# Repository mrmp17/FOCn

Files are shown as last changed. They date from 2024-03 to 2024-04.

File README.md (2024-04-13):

# FOCn - BLDC driver module

A *SimpleFOC* compatible medium-power BLDC driver module with Wi-Fi and Bluetooth connectivity
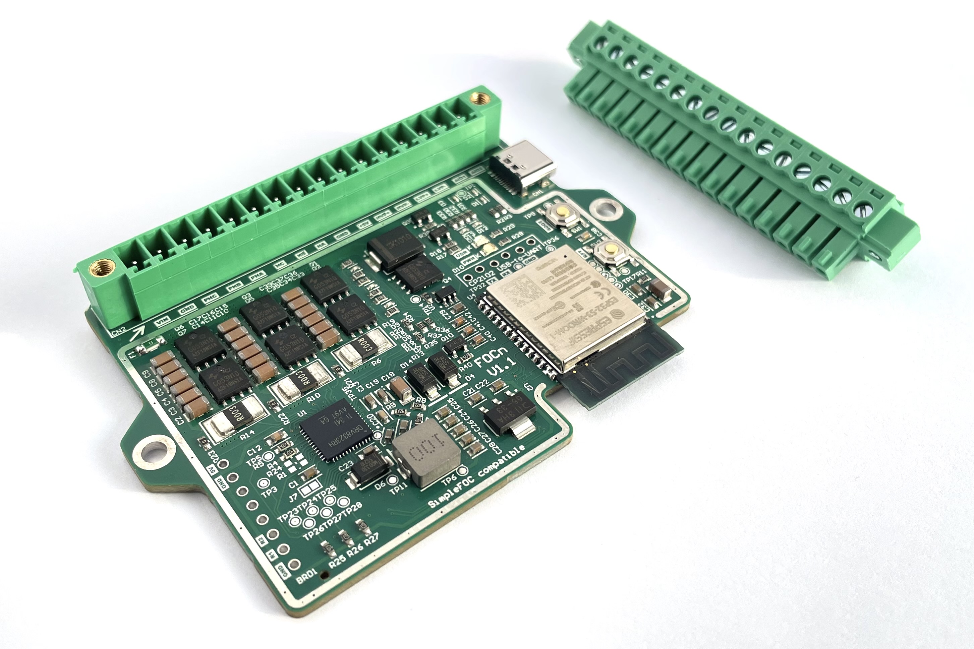
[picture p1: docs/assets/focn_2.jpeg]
FOCn photo


# Features

- Fully compatible with *SimpleFOC* field-oriented control library for easy programing
- High input voltage, up to 45V (up to 10s lithium battery)
- Up to 10A motor current without extra cooling
- Robust low-side current sensing for torque-control applications
- Supports hall sensors and encoders
- Based on ESP32-S3 dual core MCU
- Built-in USB-C and Wi-Fi / Bluetooth connectivity
- High power PWM output for solenoids, latches, magnetic brakes
- Power saving features for battery operation
- Pluggable terminal block for easy and robust connections

# Specs

- Input voltage: 9V-45V (3s - 10s lithium)
- Input current: 10A const., fuse protected
- Phase current: 10A const., 25A peak (more possible with enhanced cooling)
- Phase current measurement range: +-38A
- PWM output current: 5A average
- PWM load type: Supports inductive loads (flyback diode protection)
- Hall/encoder supply voltage: 5V
- Allowable external load on 5V supply: 300mA
- Idle current consumption (motor driver disabled, MCU seep sleep): <200uA
- Gate  driver with shunt amplifier: DRV8323

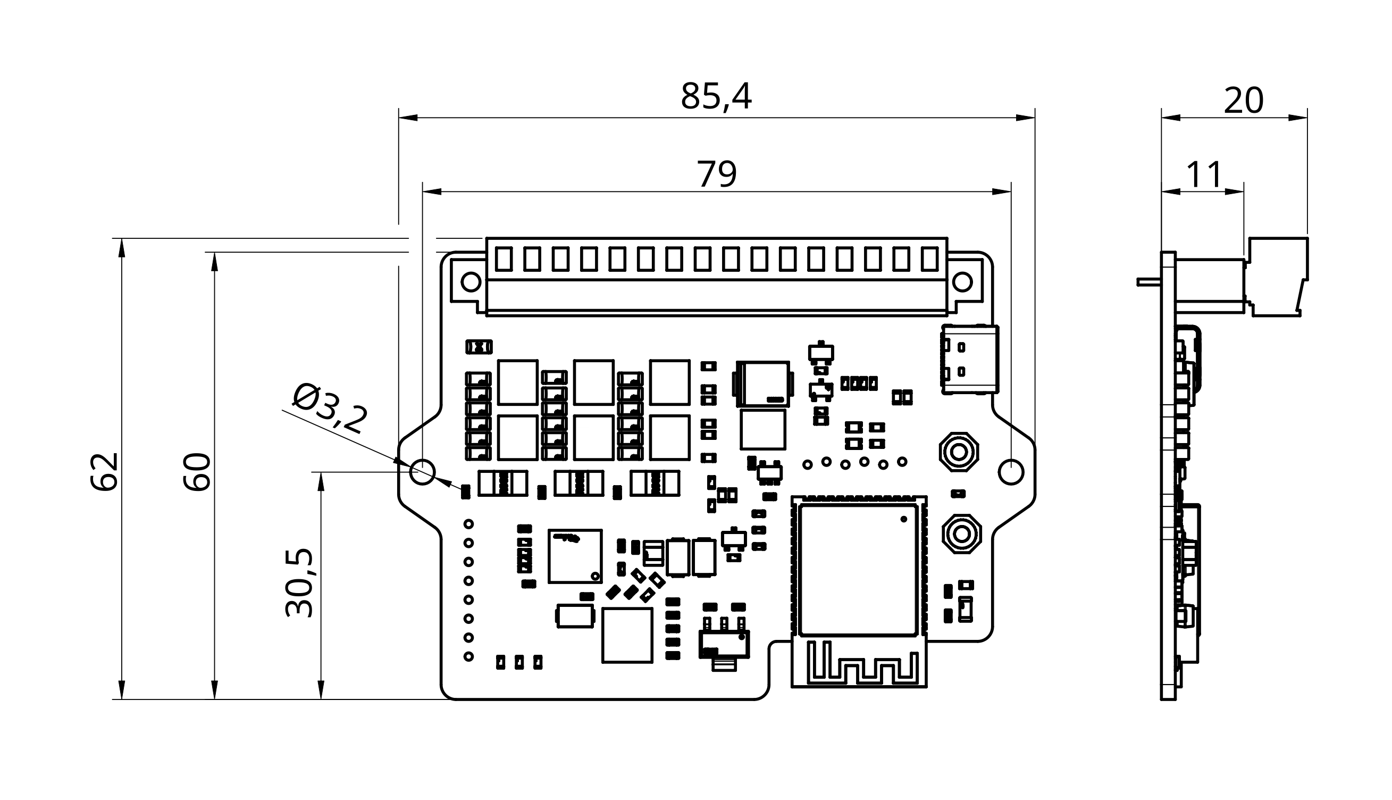
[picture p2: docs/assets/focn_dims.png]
Dimensions


# Where to get
*FOCn* is available on Tindie store.



# Getting started

### Connector pinout

Pin 1 is marked with an arrow near the connector. Compatible wire thickness is AWG18 to AWG16 (0.5 to 1.5 mm<sup>2</sup>).

| Pin | Marking | Description |
| --- | --- | --- |
| 1 | VIN | Supply voltage positive |
| 2 | GND | Supply voltage negative |
| 3 | PHC | Motor phase C |
| 4 | PHB | Motor phase B |
| 5 | PHA | Motor phase A |
| 6 | HC | Hall C / Encoder A/B |
| 7 | HB | Hall B / Encoder A/B |
| 8 | HA | Hall A / Encoder A/B |
| 9 | GND | Hall / Encoder supply voltage negative |
| 10 | +5V | Hall / Encoder supply voltage positive |
| 11 | HVP+ | High voltage PWM output positive (low side switched! HVP+ is connected to VIN) |
| 12 | HVP- | High voltage PWM output negative (low side switched!) |
| 13 | LVP+ | Low voltage PWM positive (high side switched) |
| 14 | LVP- | Low voltage PWM negative (high side switched) |
| 15 | AIO1 | Auxilary digital input 1 |
| 16 | AIO2 | Auxilary digital input 2 |

Pluggable screw terminal block part number: MAX MX15EDGKM-3.81-16P-GN01-Cu-Y-A

## Powering *FOCn*

Allowable input voltage is from 9V to 45V. Recomended cell count for lithium batteries is 3s to 10s, depending on your application. If using a power supply that is not a battery, carefully consider the effects of regenerative breaking. 

If your application requires high motor currents, consider adding an extra capacitor to the supply input, especially if other devices are powered by the same supply rail. 470uF 50V low ESR capacitor as close as possible to the input voltage terminals is recomended.

### Programming

*FOCn* can be programmed and debugged via the onboard USB-C which is connected to the ESP32’s native USB port. Programing should start automatically. If not, BOOT and RESET pushbuttons are available to control boot and programming. UART0 port is exposed on an unpopulated header.

### Motor connection

Motor phases should be connected at the screw terminal. Wiring should be as short as possible.

### Position sensors

Hall sensors or encoders with AB output can be connected to HA, HB, HC inputs. Inputs are filtered to avoid glitches caused by switching noise coupling to singal lines and strongly pulled up to 3.3V (MCU IO voltage). Pull-up voltage can be disabled from software for power saving during deep sleep.

HA, HB, HC inputs can also be used as general purpose IO by jumping jumpers J1, J2, J3 on the back of the PCB. Do this only if you know exactly what you are doing! **Warning: maximum allowable voltage input if jumpers are jumped is 3.3V!**

I2C encoders are also supported. Connect the data lines to AUX inputs.

### HVP output

High-voltage PWM is a low-side switched output designed for auxilary loads such as solenoids, magnetic brakes, indicator lights and other auxilary loads at up to 5A average current. Voltage is unregulated (same as input voltage to *FOCn*). Output can be used safely with inductive loads.

### LPV output

Low-voltage PWM is a high-side switched output designed for small auxilary loads such as sensors, indicator lights and communication modules. Up to 300mA is allocated for external loads. LVP can also be used to disable hall / encoder power for lower sleep current consumption.

### AUX inputs

Two auxilary inputs are available to be used with various sensors, safety switches, etc. Inputs are pulled up to 3.3V to support switches and open-drain outputs commonly used in industrial sensors. Maximum allowable voltage on auxilary inputs is 24V. To use auxilary inputs as outputs or data lines for I2C encoders, jump J4 and J5 on the back side of the PCB. This jumps the series protection resistor and provides a direct connection to MCU (3.3V signal level). **Warning: maximum allowable voltage input if jumpers are jumped is 3.3V!**

### RF keyfob receiver module

Keyfob remote module can be added to *FOCn*. The unpopulated header (bottom left) is designed to accept a HCS-300 rolling code receiver module. Two digital signals are connected to the MCU (D1 and D2). (module available here: https://www.parallax.com/product/key-fob-remote-and-receiver-pcb/)

### Wireless communication (Wi-Fi / BT)

The ESP32-S3 module has a built-in Wi-Fi and BLE modem which can be used to communicate with and control *FOCn*. ESP32-S3 also supports Espressif’s ESP-NOW protocol which is very suitable for BLDC control due to low latency and processing overhead. If possible, run communication and BLDC driver code on sepparate CPU cores.

### Adding extra cooling

If prolonged high motor currents (>10A) and/or high ambient temperatures (>35degC) are expected, aditional cooling should be added. This can be done by attaching a heat-dissipating body to the back of *FOCn* with a thermal pad (most heat is produced below the MOSFETs) or forced air cooling (fan)

### Using *FOCn* with smaller motors

In some cases, current sensing resolution might become an issue with low phase currents on small motors, as *FOCn* is designed for higher currents. This can be mitigated by changing the shunt resistor amplifier gain. By jumping *J7*, the gain is set to 40 (20 is default), which doubles the resolution. Keep in mind that this reduces the current measurement range to half the default value. Make sure to also modify the gains in *SimpleFOC* config.

### MCU pin mapping

| Name | GPIO | Description |
| --- | --- | --- |
| USR-LED | IO46 | User LED (yellow) |
| GDRV-INHA | IO12 | Phase A PWM |
| GDRV-INHB | IO13 | Phase B PWM |
| GDRV-INHC | IO14 | Phase C PWM |
| SHUNT-AMP-OUT-A | IO4 | Phase A current analog signal |
| SHUNT-AMP-OUT-B | IO6 | Phase B current analog signal |
| SHUNT-AMP-OUT-C | IO5 | Phase C current analog signal |
| HVPWM-CTRL | IO35 | HVPWM PWM control signal |
| LVPWM-CTRL | IO47 | LVPWM PWM control signal |
| N-HALL-PU-EN | IO48 | Hall pullup voltage enaple (active low) |
| GDRV-ENABLE | IO41 | Gate driver enable (enables BLDC driver) |
| GDRV-nFAULT | IO42 | Gate driver fault flag (active low) |
| GDRV-AMP-CAL | IO40 | Shunt amplifier offset calibration trigger |
| HALL-A | IO38 | Hall A signal |
| HALL-B | IO37 | Hall B signal |
| HALL-C | IO36 | Hall C signal |
| AUX-1 | IO10 | AUX-1 signal |
| AUX-2 | IO9 | AUX-2 signal |
| VIN-MEAS | IO8 | Suply voltage measurement analog input |
| RF-REMOTE-D1 | IO1 | RF remote module D1 signal |
| RF-REMOTE-D1 | IO2 | RF remote module D2 signal |
| TP-IO3 | IO3 | TP36 test point |
| TP-IO7 | IO7 | TP31 test point |
| TP-IO11 | IO11 | TP32 test point |
| TP-IO15 | IO15 | TP33 test point |
| TP-IO16 | IO16 | TP34 test point |
| TP-IO17 | IO17 | TP29 test point |
| TP-IO18 | IO18 | TP30 test point |

### Example project
Example *PlatformIO* project is available in the *Examples* folder. It implements basic control of a hoverboard hub motor (with phase current control) and demonstrates basic usage of *FOCn*. As the motor control input, a standard RC PWM signal is used. When developing your own projects, it is recomended to use the *PlatformIO* board file used in the example project (*/boards/FOCn_board.json*).

### Use case example
*FOCn* is used as a controller in my HoverGate project - an outdoor wing gate automated with hoverboard motors. 

Demonstration video: https://www.youtube.com/watch?v=YPjKRgDzimE

Code: https://github.com/mrmp17/HoverGate-V2-FW

Each gate wing has a *FOCn* module driving a hoverboard motor that moves the gate. To synchronize the movements, both *FOCns* communicate via ESP-NOW protocol. One of the modules also connects to Wi-Fi and is accessible on Home Assistant via MQTT. There is also an RF receiver module connected to one module so that the gates can be opened by a keyfob remote. To lock the gate wings in place when closed, a magnetic door latch is connected to the *FOCn's* high voltage PWM output.

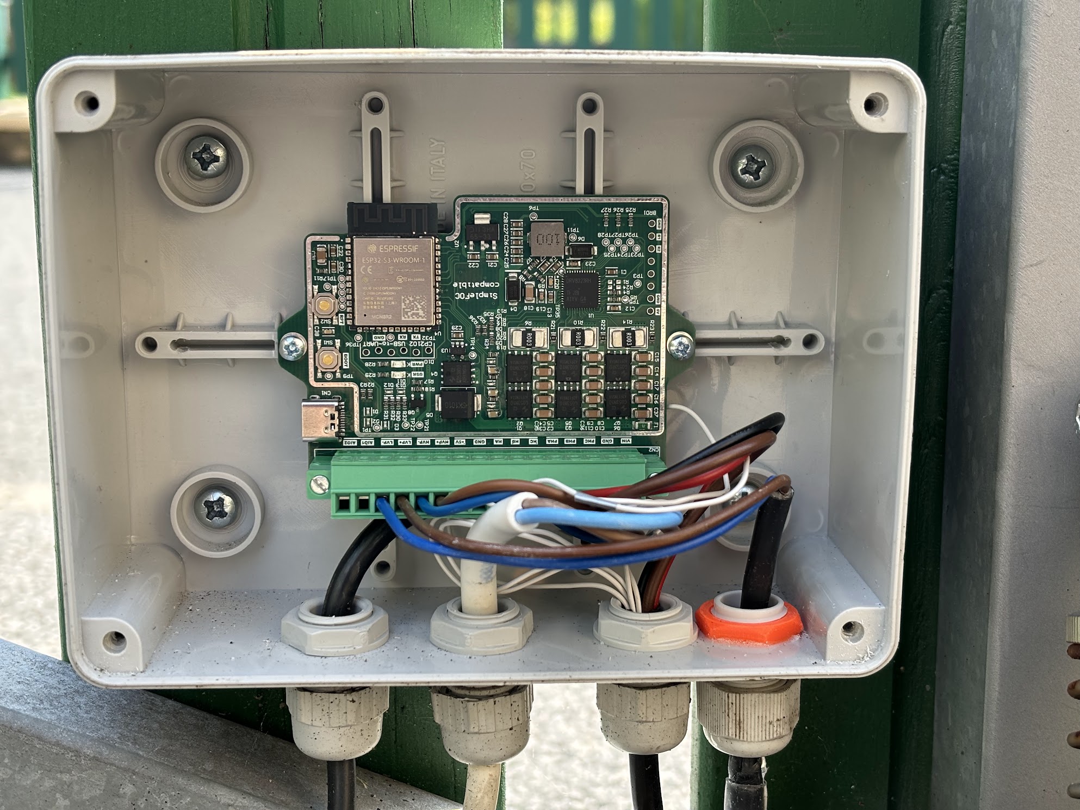
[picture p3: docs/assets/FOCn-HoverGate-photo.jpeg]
FOCn HoverGate photo


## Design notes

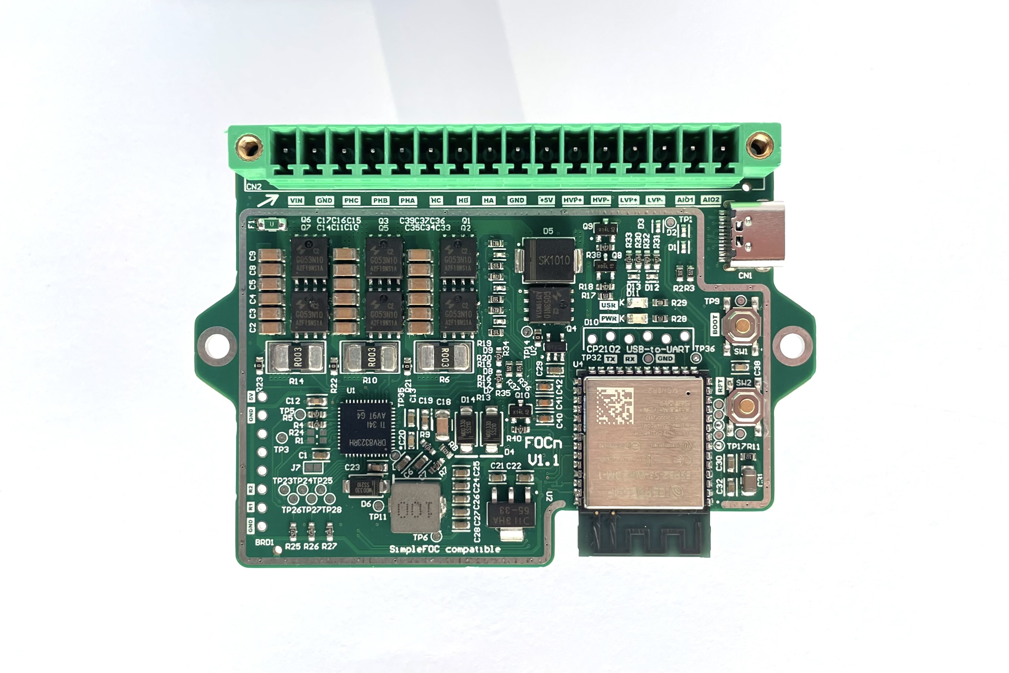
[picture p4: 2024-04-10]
docs/assets/focn_1.jpeg

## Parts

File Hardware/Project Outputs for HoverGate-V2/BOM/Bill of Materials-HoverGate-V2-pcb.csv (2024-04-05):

Comment | Description | Designator | Footprint | LibRef | Quantity | LCSC
HCS-301-rolling-code-rx |  | BRD1 | HC301-module | HCS-301-rolling-code-rx | 1
CL10A105KB8NNNC | CAP CER 1UF 50V X5R 0603 | C1, C6, C7, C13, C21, C22, C24, C25, C26, C27, C28, C29, C30, C32 | FP-CL10B105KO8NNNC-IPC_B | CMP-2000-06093-2 | 14 | C15849
CL31A106KBHNNNE | CAP CER 10UF 50V X5R 1206 | C2, C3, C4, C5, C8, C9, C10, C11, C14, C15, C16, C17, C33, C34, C35, C36, C37, C39 | FP-CL31-IPC_C | CMP-13271-000016-1 | 18 | C13585
CL10B104KC8NNNC | Cap Ceramic 100nF 100V X7R ±10% Pad SMD 0603 +125°C T/R | C12, C19, C23 | FP-CL10-IPC_A | CMP-13271-004036-1 | 3
GRM32ER71J106KA12L | CAP CER 10UF 63V X7R 1210 | C18 | FP-GRM32E-0_2-0_3-MFG | CMP-2000-07458-2 | 1 | C437568
AC0603KRX7R0BB473 | CAP CER 0.047UF 100V X7R 0603 | C20, C38 | FP-AC0603-IPC_B | CMP-03422-001184-1 | 2 | C469624
CL31A226KPHNNNE | Cap Ceramic 22uF 10V X5R ±10% SMD 1206 | C31 | FP-CL31-IPC_B | CMP-13271-002604-1 | 1 | C5672
0603B151K500NT | CAP CER 150p 50V X7R 0603 | C40, C41, C42 | FP-AC0603-IPC_B | CMP-03422-001184-1 | 3 | C1594
XKB U262-161N-4BVC11 | USB Type-C connector, USB-2.0, 16 pins | CN1 | XKB U262-161N-4BVC11 | XKB U262-161N-4BVC11 | 1 | C319148
MAX MX15EDGVM-3.81-16P-GN01-Cu-A | Board connector for 16 pin pluggable screw terminal | CN2 | MAX MX15EDGVM-3.81-16P-GN01-Cu-A | MAX MX15EDGVM-3.81-16P-GN01-Cu-A | 1 | C5188240
CP2102 USB-A-to-UART adapter connector |  | CN3 | CP2102 USB-A-to-UART adapter connector | CP2102 USB-A-to-UART adapter connector | 1
LXES15AAA1-133 | TVS DIODE 15V 1005 | D1, D2, D3, D7, D8, D9, D12, D13 | FP-LXES15-IPC_A | CMP-06195-000011-1 | 8 | C191267
B1100-13-F | Schottky Barrier Rectifier, 100 V, 1 A, -65 to 150 degC, 2-Pin SMA, RoHS, Tape and Reel | D4, D6, D14 | DIOD-SMA-2_V | CMP-2000-05882-1 | 3 | C110106
SK1010C | DIODE SCHOTTKY 100V 10A SMC | D5 | FP-SMC-MFG | CMP-2000-05097-3 | 1 | C3018527
KT-0805G | KT-0805G LED Green | D10 | LED_0805 | LED Green | 1 | C2297
KT-0805Y | LED Yellow KT-0805Y | D11 | LED_0805 | LED Blue | 1 | C2296
0458005.DR | FUSE BOARD MOUNT 5A 75VDC 1206 | F1 | FP-0469-IPC_B | CMP-08605-000100-1 | 1 | C187561
SolderJumperV2 |  | J1, J2, J3, J4, J5, J6, J7 | AislerRule_SolderJumper_1mm | SolderJumperV2 | 7
CYA0630-10UH | SMD Power inductio, 10uH 4A | L1 | CYA0630-10UH | PowerInductor | 1 | C5189958
HYG053N10NS1C2 | 100V 95A 4.6mOhm N-channel mosfet | Q1, Q2, Q3, Q4, Q5, Q6, Q7 | PDFN5*6-8L | HYG053N10NS1C2 | 7
BM3402 | BORN BM3402 MOSFET N-CH 30V 5.1A SOT23 | Q8 | FP-SOT23-IPC_B | CMP-83955-000006-1 | 1 | C431498
AO3401A | P-Channel MOSFET, 30 V, 4 A, -55 to 150 degC, 3-Pin SOT-23-3L, RoHS, Tape and Reel | Q9, Q10 | AO-SOT-23-3L_V | CMP-2000-05778-1 | 2
DNP | RES SMD 47K OHM 1% 1/10W 0603 | R1, R24 | FP-RC0603FR-0747KL-MFG | CMP-1659-00055-2 | 2 | C105579
0603WAF5101T5E |  | R2, R3, R11, R13, R16, R17, R20, R28, R36, R37 | RESC1608X55X30NL15T15 | CMP-2000-00540-1 | 10 | C23186
RC0603FR-0747KL | RES SMD 47K OHM 1% 1/10W 0603 | R4, R5, R7, R9, R18, R25, R26, R27, R30, R31, R32, R33, R34, R35, R38, R40 | FP-RC0603FR-0747KL-MFG | CMP-1659-00055-2 | 16 | C105579
LR2512D-3W-3mR-1% | 2512 3mohm shunt | R6, R10, R14 | FPR_CRF2512_R0 | R | 3 | C500737
0603WAF2203T5E |  | R8 | RESC1608X55X30NL15T15 | CMP-2000-00540-1 | 1 | C22961
0603WAF8200T5E |  | R12, R15, R19 | RESC1608X55X30NL15T15 | CMP-2000-00540-1 | 3 | C23253
0603WAF0000T5E | 0R resistor | R21, R22, R23, R39 | FPR_0603_R_R0 | R | 4
0603WAF1001T5E |  | R29 | RESC1608X55X30NL15T15 | CMP-2000-00540-1 | 1 | C21190
TS-1187A-B-A-B | XKB TS-1187A-B-A-B C318884 | SW1, SW2 | ESWI-TL3342F160QG_V | CMP-1696-00003-1 | 2 | C318884
test point 1.5mm | Test point ,1.5mm diameter, no hole | TP1, TP2, TP3, TP4, TP5, TP6, TP7, TP8, TP9, TP10, TP11, TP12, TP13, TP14, TP15, TP16, TP17, TP18, TP19, TP20, TP23, TP24, TP25, TP26, TP27, TP28, TP29, TP30, TP31, TP32, TP33, TP34, TP35, TP36 | TP1_FULL | Test Point | 34
DRV8323RHRGZT | IC MTR DRV MULTIPHAS 6-60V 48QFN | U1 | FP-RGZ0048A-IPC_A | CMP-04912-000089-1 | 1
AP7365-33EG-13 | IC REG LIN 3.3V 600MA SOT223-3 | U2 | FP-SOT223-IPC_C | CMP-12756-000040-1 | 1
SLM27517 | mosfet gate driver | U3 | Diodes Inc SOT25 | SLM27517 | 1
ESP32-S3-WROOM-1-N8R2 | WiFi 802.11a/b/g/n, Bluetooth v5.0 Transceiver Module 2.4GHz Antenna Not Included - | U4 | XCVR_ESP32-S3-WROOM-1-N8R2 | ESP32-S3-WROOM-1-N8R2 | 1

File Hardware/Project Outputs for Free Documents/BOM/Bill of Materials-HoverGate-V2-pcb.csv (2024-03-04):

Comment | Description | Designator | Footprint | LibRef | Quantity | LCSC
HCS-301-rolling-code-rx |  | BRD1 | HC301-module | HCS-301-rolling-code-rx | 1
CL10A105KB8NNNC | CAP CER 1UF 50V X5R 0603 | C1, C6, C7, C13, C21, C22, C24, C25, C26, C27, C28, C29, C30, C32, C33, C34 | FP-CL10B105KO8NNNC-IPC_B | CMP-2000-06093-2 | 16 | C15849
GRM32ER71J106KA12L | CAP CER 10UF 63V X7R 1210 | C2, C3, C4, C5, C8, C9, C10, C11, C14, C15, C16, C17, C18, C35, C36, C37 | FP-GRM32E-0_2-0_3-MFG | CMP-2000-07458-2 | 16 | C437568
CL10B104KC8NNNC | Cap Ceramic 100nF 100V X7R ±10% Pad SMD 0603 +125°C T/R | C12, C19, C23 | FP-CL10-IPC_A | CMP-13271-004036-1 | 3
AC0603KRX7R0BB473 | CAP CER 0.047UF 100V X7R 0603 | C20, C38 | FP-AC0603-IPC_B | CMP-03422-001184-1 | 2 | C469624
CL31A226KPHNNNE | Cap Ceramic 22uF 10V X5R ±10% SMD 1206 | C31 | FP-CL31-IPC_B | CMP-13271-002604-1 | 1 | C5672
XKB U262-161N-4BVC11 | USB Type-C connector, USB-2.0, 16 pins | CN1 | XKB U262-161N-4BVC11 | XKB U262-161N-4BVC11 | 1 | C319148
MAX MX15EDGVM-3.81-16P-GN01-Cu-A | Board connector for 16 pin pluggable screw terminal | CN2 | MAX MX15EDGVM-3.81-16P-GN01-Cu-A | MAX MX15EDGVM-3.81-16P-GN01-Cu-A | 1 | C5188240
CP2102 USB-A-to-UART adapter connector |  | CN3 | CP2102 USB-A-to-UART adapter connector | CP2102 USB-A-to-UART adapter connector | 1
LXES15AAA1-133 | TVS DIODE 15V 1005 | D1, D2, D3, D7, D8, D9, D12, D13 | FP-LXES15-IPC_A | CMP-06195-000011-1 | 8 | C191267
B1100-13-F | Schottky Barrier Rectifier, 100 V, 1 A, -65 to 150 degC, 2-Pin SMA, RoHS, Tape and Reel | D4, D6 | DIOD-SMA-2_V | CMP-2000-05882-1 | 2 | C110106
SK1010C | DIODE SCHOTTKY 100V 10A SMC | D5 | FP-SMC-MFG | CMP-2000-05097-3 | 1 | C3018527
LED Green | Generic LED Green | D10 | LED_0805 | LED Green | 1
LED Blue | LED Blue | D11 | LED_0805 | LED Blue | 1
0458005.DR | FUSE BOARD MOUNT 5A 75VDC 1206 | F1 | FP-0469-IPC_B | CMP-08605-000100-1 | 1 | C187561
SolderJumperV2 |  | J1, J2, J3, J4, J5 | AislerRule_SolderJumper_1mm | SolderJumperV2 | 5
CYA0630-10UH | SMD Power inductio, 10uH 4A | L1 | CYA0630-10UH | PowerInductor | 1 | C5189958
HYG053N10NS1C2 | 100V 95A 4.6mOhm N-channel mosfet | Q1, Q2, Q3, Q4, Q5, Q6, Q7 | PDFN5*6-8L | HYG053N10NS1C2 | 7
BM3402 | BORN BM3402 MOSFET N-CH 30V 5.1A SOT23 | Q8 | FP-SOT23-IPC_B | CMP-83955-000006-1 | 1 | C431498
DNP | RES SMD 47K OHM 1% 1/10W 0603 | R1, R24 | FP-RC0603FR-0747KL-MFG | CMP-1659-00055-2 | 2 | C105579
0603WAF5101T5E |  | R2, R3, R8, R9, R11, R12, R13, R15, R16, R17, R19, R20, R28, R29, R36, R37 | RESC1608X55X30NL15T15 | CMP-2000-00540-1 | 16 | C23186
RC0603FR-0747KL | RES SMD 47K OHM 1% 1/10W 0603 | R4, R5, R7, R18, R25, R26, R27, R30, R31, R32, R33, R34, R35 | FP-RC0603FR-0747KL-MFG | CMP-1659-00055-2 | 13 | C105579
LR2512D-3W-3mR-1% | 2512 3mohm shunt | R6, R10, R14 | FPR_CRF2512_R0 | R | 3 | C500737
0R | 0R resistor | R21, R22, R23 | FPR_0603_R_R0 | R | 3
TS-1187A-B-A-B | XKB TS-1187A-B-A-B C318884 | SW1, SW2 | ESWI-TL3342F160QG_V | CMP-1696-00003-1 | 2 | C318884
test point 1.5mm | Test point ,1.5mm diameter, no hole | TP1, TP2, TP3, TP4, TP5, TP6, TP7, TP8, TP9, TP10, TP11, TP12, TP13, TP14, TP15, TP16, TP17, TP18, TP19, TP20, TP21, TP22, TP23, TP24, TP25, TP26, TP27, TP28, TP29, TP30, TP31, TP32, TP33, TP34, TP35, TP36 | TP1_FULL | Test Point | 36
DRV8323RHRGZT | IC MTR DRV MULTIPHAS 6-60V 48QFN | U1 | FP-RGZ0048A-IPC_A | CMP-04912-000089-1 | 1
AZ1117CH-3.3TRG1 | IC REG LINEAR 3.3V 800MA SOT223 | U2 | FP-SOT223-IPC_B | CMP-12756-000028-1 | 1 | C92102
MCP1402T-E/OT | Tiny 500 mA, High-Speed Power MOSFET Driver, Non Inverting, Extended Temperature, Tape and Reel | U3 | SOT-23-OT5_L | CMP-0137-00408-1 | 1 | C128573
ESP32-S3-WROOM-1-N8R2 | WiFi 802.11a/b/g/n, Bluetooth v5.0 Transceiver Module 2.4GHz Antenna Not Included - | U4 | XCVR_ESP32-S3-WROOM-1-N8R2 | ESP32-S3-WROOM-1-N8R2 | 1
AZ1117CH-5.0TRG1 | IC REG LINEAR 5.0V 800MA SOT223 | U5 | FP-SOT223-IPC_B | CMP-12756-000028-1 | 1 | C99342

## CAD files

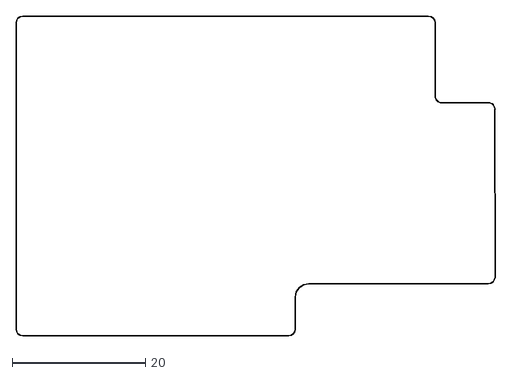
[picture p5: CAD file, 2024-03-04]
Hardware/3d/fancyedge.dxf
72.0 x 48.0

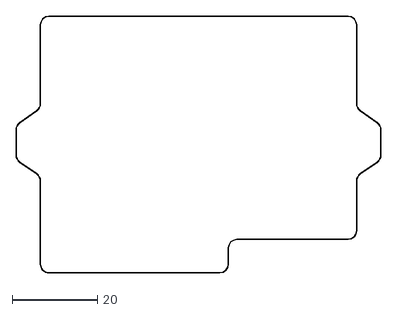
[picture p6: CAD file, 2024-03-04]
Hardware/3d/PCB-shape.dxf
85.4 x 60.0

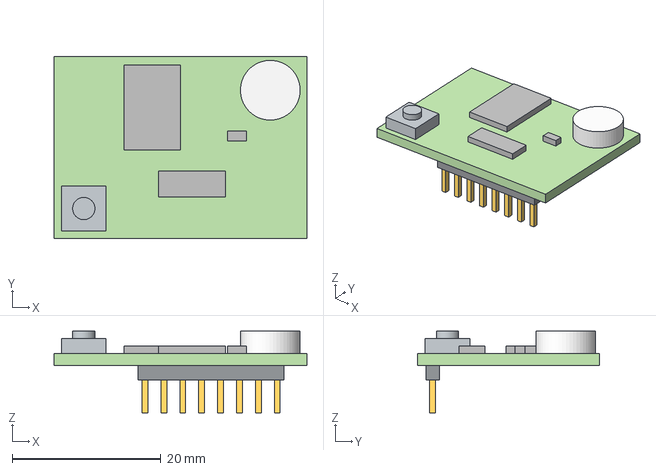
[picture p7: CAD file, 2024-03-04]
Hardware/3d/hcs301-module.step
34.0 x 24.4 x 11.0 mm

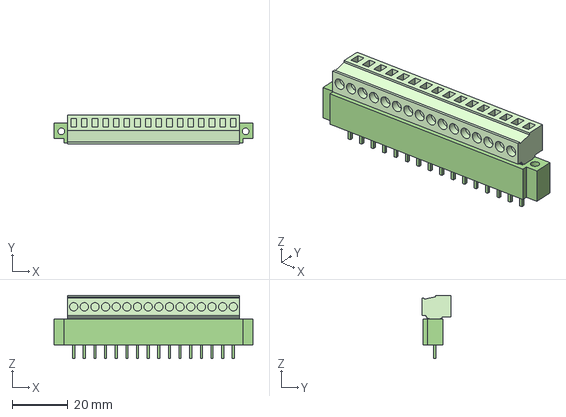
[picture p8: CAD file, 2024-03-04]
Hardware/3d/MAX MX15EDGVM-3.81-16P.step
71.2 x 10.4 x 22.7 mm

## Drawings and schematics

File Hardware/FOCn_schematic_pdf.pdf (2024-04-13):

# VBUS A9 SHELL SHELL SHELL SHELL TYPE-C USB-2.0 CN1

# USB-C connector (ESP debug & comms)

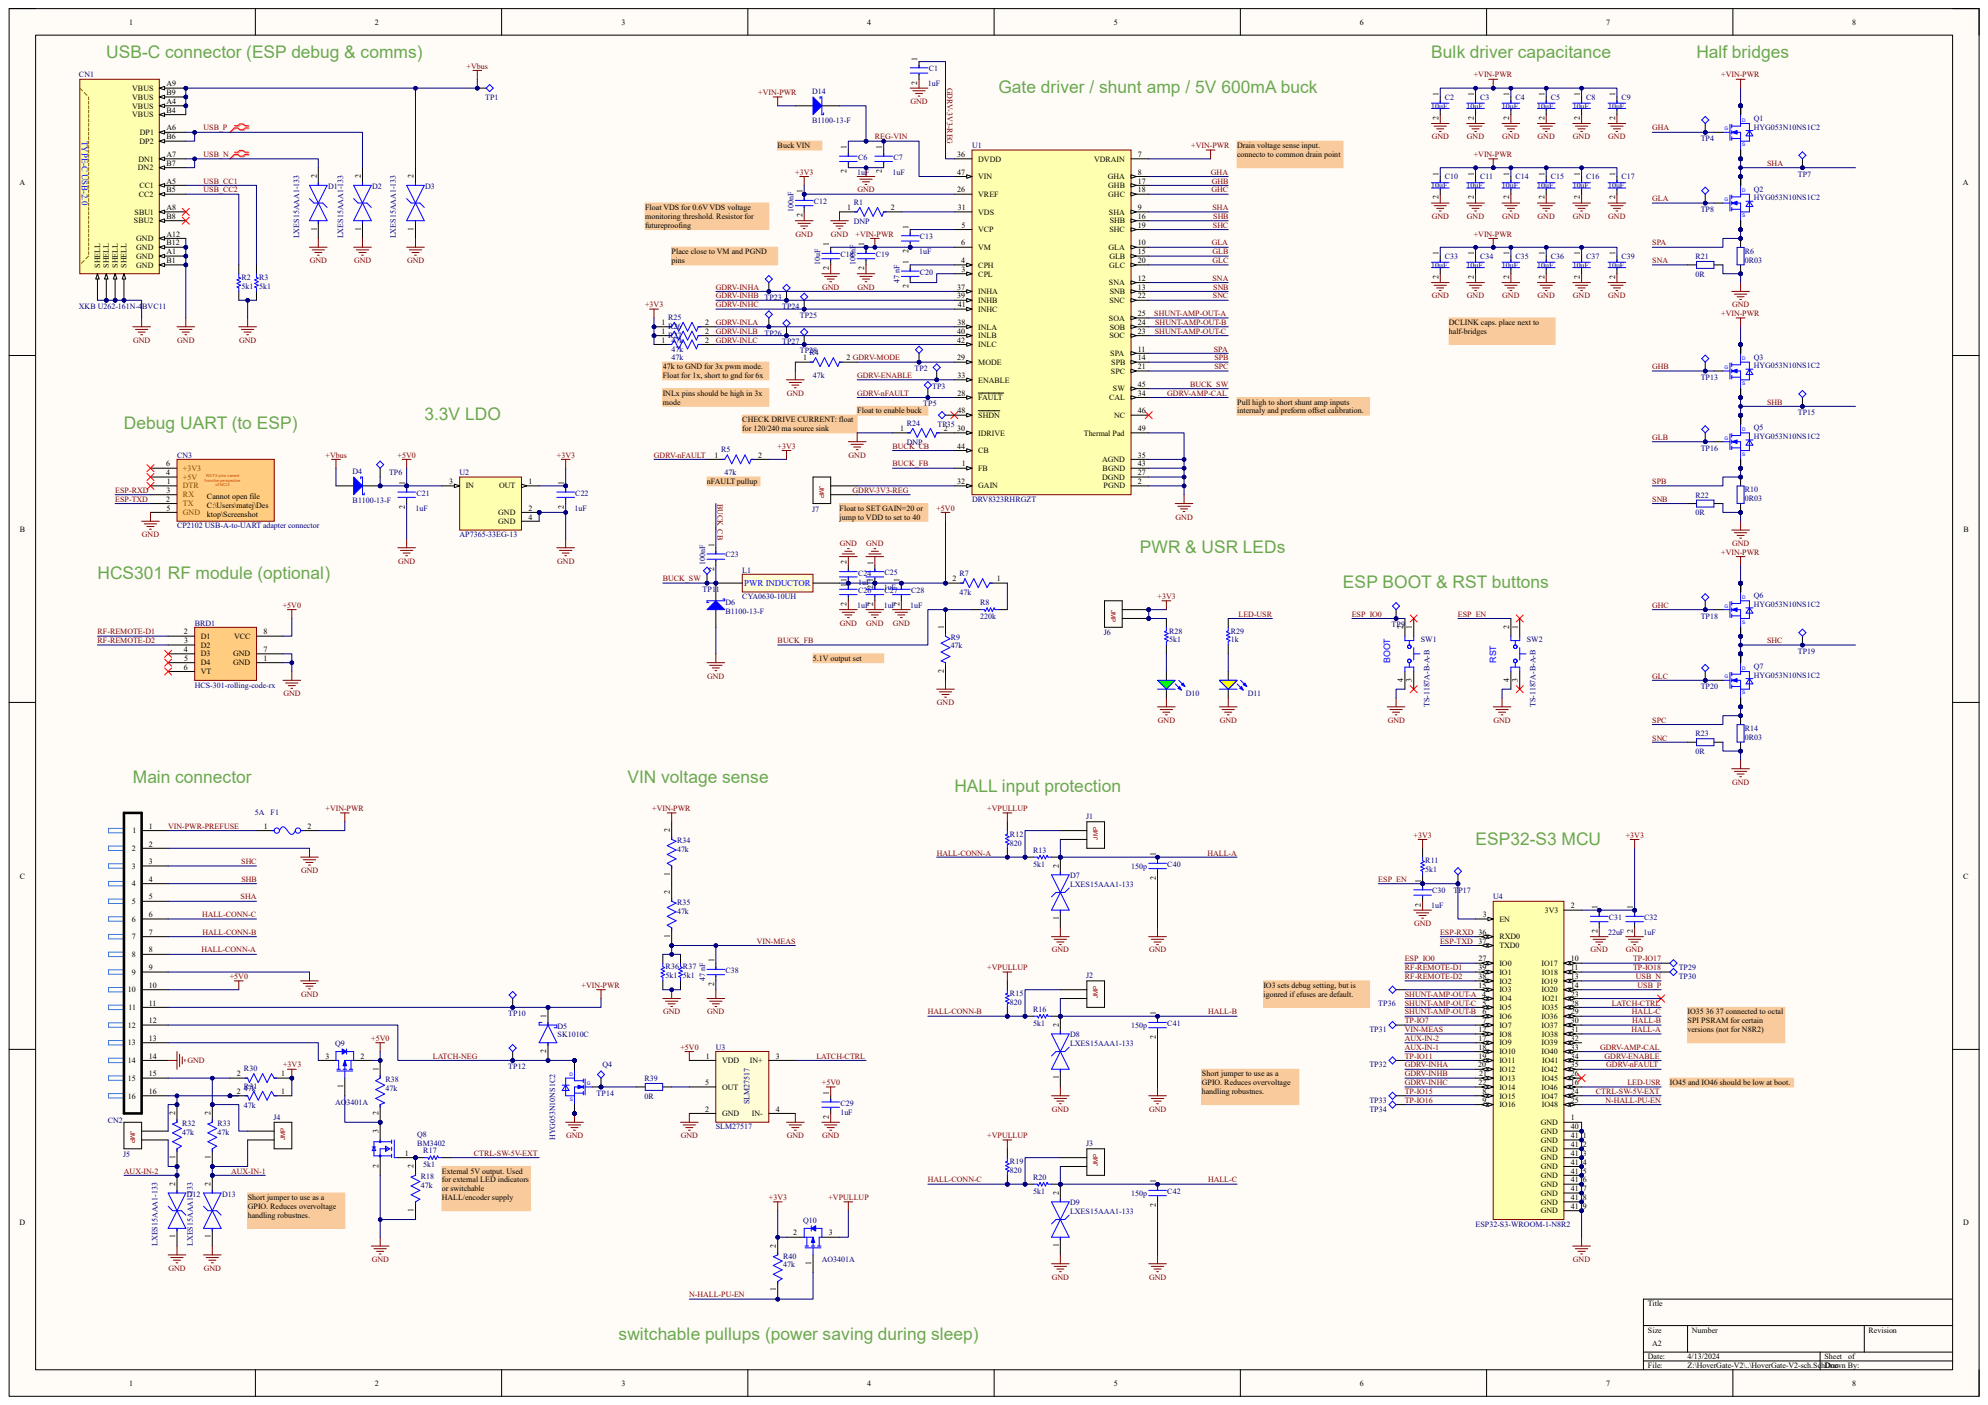
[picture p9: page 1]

Gate driver / shunt amp / 5V 600mA buck

+VIN-PWR Drain voltage sense input.

connecto to common drain point

Float VDS for 0.6V VDS voltage
monitoring threshold. Resistor for
futureproofing

Place close to VM and PGND
pins

DCLINK caps. place next to
half-bridges

Pull high to short shunt amp inputs

3.3V LDO Debug UART (to ESP)

CHECK DRIVE CURRENT: float
for 120/240 ma source sink

Float to enable buck

RX/TX pins named
from the perspective
of MCU!
Cannot open file
C:\Users\matej\Des
ktop\Screenshot

Float to SET GAIN=20 or
jump to VDD to set to 40

CP2102 USB-A-to-UART adapter connector

ESP BOOT & RST buttons

HCS-301-rolling-code-rx

IO3 sets debug setting, but is
igonred if efuses are default.

IO35 36 37 connected to octal
SPI PSRAM for certain
versions (not for N8R2)

Short jumper to use as a
GPIO. Reduces overvoltage
handling robustnes.

IO45 and IO46 should be low at boot.

switchable pullups (power saving during sleep)

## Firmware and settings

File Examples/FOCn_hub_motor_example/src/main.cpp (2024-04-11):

#include <Arduino.h>
#include "SimpleFOC.h"

#define usr_led_pin 46
#define aux1_pin 10
#define pullup_en_pin 48

// ########## set motor parameters here ##########
// power supply voltage
#define drv_power_sply 15.0f
// limits max voltage at the motor (set to input voltage if not needed)
#define drv_driver_volt_limit 8.0f
// voltage used for hall sensor alignment. Start low and increase until align is reliable
#define drv_align_voltage 2.0f
#define drv_polePairs 15
// ########## end motor parameters #########


#define drv_pwmA_pin 12
#define drv_pwmB_pin 13
#define drv_pwmC_pin 14
#define drv_enable_pin 41
#define drv_snsA_pin 4
#define drv_snsB_pin 6
#define drv_snsC_pin 5
#define drv_hallA_pin 38
#define drv_hallB_pin 37
#define drv_hallC_pin 36
#define drv_cal_pin 40
#define drv_shunt_res 0.003f
#define drv_shunt_gain (-20.0f)

#define hvpwm_pin 35
#define lvpwm_pin 47


// ########## set max motor target value here ##########
#define drv_target_max 15.0f




//simplefoc motor
static BLDCMotor drv_motor = BLDCMotor(drv_polePairs);
//simplefoc driver
static BLDCDriver3PWM drv_driver = BLDCDriver3PWM(drv_pwmA_pin, drv_pwmB_pin, drv_pwmC_pin, drv_enable_pin);
//simplefoc hall sensor
static HallSensor drv_sensor = HallSensor(drv_hallA_pin, drv_hallB_pin, drv_hallC_pin, drv_polePairs);
//simplefoc current sensor
static LowsideCurrentSense drv_current_sense = LowsideCurrentSense(drv_shunt_res, drv_shunt_gain, drv_snsA_pin, drv_snsB_pin, drv_snsC_pin);

// HALL interrupt routine initialization
void drv_int_hall_A(){drv_sensor.handleA();}
void drv_int_hall_B(){drv_sensor.handleB();}
void drv_int_hall_C(){drv_sensor.handleC();}



// RC PWM stuff ---------------------
volatile uint32_t PwmRiseTime = 0;
volatile uint32_t PwmTimeNow = 0;
volatile uint32_t PwmPulseTime = 0;
volatile uint32_t PwmLastEdge = 0;
volatile bool PwmValid = false;
// map RC PWM pulse time to motor target value
float mapFloat(float x, float in_min, float in_max, float out_min, float out_max) {
    return (x - in_min) * (out_max - out_min) / (in_max - in_min) + out_min;
}
float rcPwmToMotorTarget(float rcPwm){
  return mapFloat(rcPwm, 1100.0, 1800.0, -drv_target_max, drv_target_max);
}

// PWM interrupt
void IRAM_ATTR pwmInInterrupt() {
  PwmTimeNow = micros();
  PwmLastEdge = PwmTimeNow;
  if(digitalRead(aux1_pin) == HIGH){
    //rising edge
    PwmRiseTime = PwmTimeNow;
  }
  else{
    //falling edge
    PwmPulseTime = PwmTimeNow - PwmRiseTime;
    if(PwmPulseTime > 1000 && PwmPulseTime < 2000){
      PwmValid = true;
    }
    else{
      PwmValid = false;
    }
  }
}
// End RC PWM stuff ---------------------


void setup() {
  Serial.begin(115200);
  delay(4000);
  Serial.println("Hello FOCn boot ok!!");
  // put your setup code here, to run once:
  pinMode(usr_led_pin, OUTPUT);
  pinMode(drv_cal_pin, OUTPUT);
  pinMode(pullup_en_pin, OUTPUT);


  //enable hall pullups
  digitalWrite(pullup_en_pin, LOW);

  // gate driver can calibrate shunt amp offsets. If needed do this after every gate driver enable:
  // digitalWrite(drv_cal_pin, HIGH);
  // delay(2); //calibration takes 100us as per datasheet
  // digitalWrite(drv_cal_pin, LOW);
  // delay(2); //settle back to normal amplification

  // if analogRead is not called on ADC pins, ESP crashes when SimpleFOC starts sampling
  // This seems to be a ESP32-S3 SimpleFOC issue
  analogRead(drv_snsA_pin);
  analogRead(drv_snsB_pin);
  analogRead(drv_snsC_pin);

  //enable simplefoc debug
  SimpleFOCDebug::enable();

  // initialize hall sensor hardware
  drv_sensor.init();
  Serial.println("sensor init done!");

  //register callbacks for hall interrupts
  drv_sensor.enableInterrupts(drv_int_hall_A, drv_int_hall_B, drv_int_hall_C);

  //link sensor to motor
  drv_motor.linkSensor(&drv_sensor);

  // set power supply voltage param
  drv_driver.voltage_power_supply = drv_power_sply;
  // limit max voltage driver can set
  drv_driver.voltage_limit = drv_driver_volt_limit;

  //init driver
  drv_driver.init();
  Serial.println("driver init done!");

  //link motor and driver
  drv_motor.linkDriver(&drv_driver);

  //voltage for hall align
  drv_motor.voltage_sensor_align = drv_align_voltage;

  //select FOC modulation
  drv_motor.foc_modulation = FOCModulationType::SpaceVectorPWM;

  //link current sense to driver
  drv_current_sense.linkDriver(&drv_driver);

  // ########## SELECT MOTION CONTROLLER HERE ##########
  // voltage is most reliable - it does not depend on current sensing
  // if set to voltage, target is voltage [V] applied to the motor
  // if set to dc/foc current, target is phase current [A] (DC or FOC q component)
  // ###
  // drv_motor.torque_controller = TorqueControlType::voltage;
  // drv_motor.torque_controller = TorqueControlType::dc_current;
  drv_motor.torque_controller = TorqueControlType::foc_current;
  // ###

  //select motion controller
  drv_motor.controller = MotionControlType::torque;

  //init motor
  drv_motor.init();
  Serial.println("M: motor init done!");

  // init current sense
  if (drv_current_sense.init())  Serial.println("Current sense init success!");
  else{
      Serial.println("Current sense init failed!");
      while(1){
        //stop here if failed
        delay(100);
      }
  }

  //link current sense to motor
  drv_motor.linkCurrentSense(&drv_current_sense);

  // ########## select if you want to skip current sense alignment ##########
  // pins and gains need to be set correctly to do this. For basic FOCn you can skip this,
  // ### 
  drv_current_sense.skip_align = true;
  // ###

  // ########## select if you want to skip hall sensor alignment ##########
  // direction and offset angle needs to be set correctly to do this. Use automatic alignment when starting to get values.
  // ###
  // select one direction
  // drv_motor.sensor_direction = Direction::CW;
  // drv_motor.sensor_direction = Direction::CCW;
  // set angle offset (in RAD)
  // drv_motor.zero_electric_angle = 4.20;
  // ###

  //init FOC
  drv_motor.initFOC();
  Serial.println("FOC init done!");

  // uncomment to print hall alignment params
  // Serial.println("automatic hall align got data:");
  // Serial.printf("Hall calib: zero: %f, dir: %d \n", drv_motor.zero_electric_angle, drv_motor.sensor_direction);
  // Serial.println("help: dir vals: 1:CW  -1:CCW  0:UNKNOWN");


  // ##### aditional hardware shunt amplifier calibration #####
  // gate driver can calibrate shunt amp offsets. If needed do this after every gate driver enable:
  // digitalWrite(drv_cal_pin, HIGH);
  // delay(2); //calibration takes 100us as per datasheet
  // digitalWrite(drv_cal_pin, LOW);
  // delay(2); //settle back to normal amplification




  // attach interrupt for RC PWM input
  attachInterrupt(digitalPinToInterrupt(aux1_pin), pwmInInterrupt, CHANGE);

  //enable driver
  drv_driver.enable();




}

void loop() {
  //timing variables for periodic events
  static uint32_t last_t = millis();
  static uint32_t last_t2 = millis();


  // SimpleFOC FOC and move handlers run in loop
  drv_motor.loopFOC();
  drv_motor.move();



  // Every 50ms event
  if(millis() - last_t2 > 50){
    last_t2 = millis();

    // parse RC PWM input and set motor target
    if(micros() - PwmLastEdge > 200000){
      Serial.println("No PWM signal");
      PwmValid = false;
    }
    else{
      // Serial.printf("PWM signal: %d us\n", PwmPulseTime);
    }


    //bldc ctrl
    if(PwmValid){
      if(PwmPulseTime > 1435 && PwmPulseTime < 1465){
        drv_motor.target = 0;
      }
      else{
        drv_motor.target = rcPwmToMotorTarget(PwmPulseTime);
        Serial.println("set to " + String(drv_motor.target));
      }
      // BLDC.set_pwm(rcPwmToMotorPwm(PwmPulseTime));
      // Serial.printf("BLDC set to %d\n", rcPwmToMotorPwm(PwmPulseTime));
    }
    else{
      drv_motor.target = 0;
    }


  }

  // Every 1s event
  if(millis() - last_t > 1000){
    last_t = millis();

    // print phase current and velocity
    Serial.println("phase current: " + String(drv_current_sense.getDCCurrent()));
    Serial.println("velocity: " + String(drv_motor.shaftVelocity()));
  }





}

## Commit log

2024-03-04 initial commit. This was first PCB made (used in HoverGateV2)
    [Bill of Materials-HoverGate-V2-pcb.csv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]
2024-03-04 stronger pullups, added dclink caps, led resistor, hall filter caps, hvpwm pulldown (sch updates)
    [HoverGate-V2-sch.SchDoc]
2024-03-04 fixed hall filter caps
    [HoverGate-V2-sch.SchDoc]
2024-03-04 pullup switch added
    [HoverGate-V2-sch.SchDoc]
2024-03-04 replaced hvpwm gate driver to reduce cost
    [HoverGate-V2-sch.SchDoc, HoverGate-V2.PrjPcb]
2024-03-05 changed 5V output to hig side switching to allow switchable hall supply. changed some component values.
    [HoverGate-V2-sch.SchDoc]
2024-03-05 change dclink cap type
    [HoverGate-V2-sch.SchDoc]
2024-03-05 made changes to pcb
    [HoverGate-V2-sch.SchDoc]
2024-03-05 pcb improvements
2024-03-19 minor improvements
    [Bill of Materials-HoverGate-V2-pcb.csv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]
2024-04-05 production files
    [Bill of Materials-HoverGate-V2-pcb.csv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]
2024-04-05 added sepparate hardware and software example folders
    [Bill of Materials-HoverGate-V2-pcb.csv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]
2024-04-05 added platformio example project, added custom board json
2024-04-09 basic hub motor FW example implemented
